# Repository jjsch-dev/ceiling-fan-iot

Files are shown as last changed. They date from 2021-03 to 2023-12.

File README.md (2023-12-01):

# Ceiling Fan Control - (No Humming)

The purpose of this project was to develop a hum-free electronic ceiling fan device that can be controlled remotely (IOT) or locally with a rotary encoder.

The selected processor was the [ESP32-C3](https://www.espressif.com/sites/default/files/documentation/esp32-c3-mini-1_datasheet_en.pdf) in its mini development kit format.

## Explode view 

As the purpose was to replace an old controller in my house, to fit it into a 100mm wall box I had to build a PCB to reduce footprint and use a 3D printer for the front cover that would fit a standard frame for electricity.

As in linux there is no support for fusion 360 use onshape to model the [assembly](https://cad.onshape.com/documents/71acf9008c56a0b1a5695f37/w/967222a47d34025a139e3862/e/0c178ba322c00475acc6add3) and cads of the [front cover](https://cad.onshape.com/documents/136d4c7a6a8e92c2be45bf03/w/4c451ab5564fe96ef80b367c/e/ab9c2ed234f4e64b43c2f324) which only requires a browser, and the result is amazing. And to design and manufacture the [PCB](https://easyeda.com/juanschiavoni/ceiling-iot-esp32-c3) use easyeda, the manufacturing service is good, but I could not export the pcba in step format, I had to use kicad.



## Electronic for No Humming

To prevent humming, capacitive reactances are used to limit the current in the motor stator, and since the friction (blades etc) is moderately high, the rotation speed decreases. This version has four speeds to keep the form factor as small as possible, (capacitors and relays are large).

## IOT Control

To control the device from a cell phone, [Espressif Rainmaker](https://rainmaker.espressif.com/docs/get-started.html) is used, which has an application for android and iphone, which allows you to configure the Wi-Fi network (provisioning), and control the device through the AWS IOT.

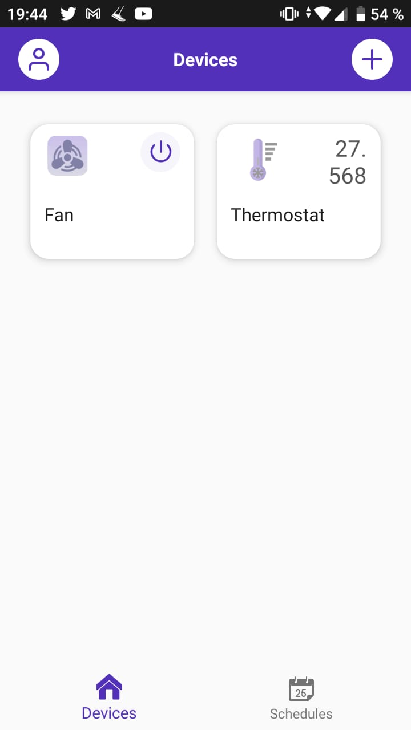
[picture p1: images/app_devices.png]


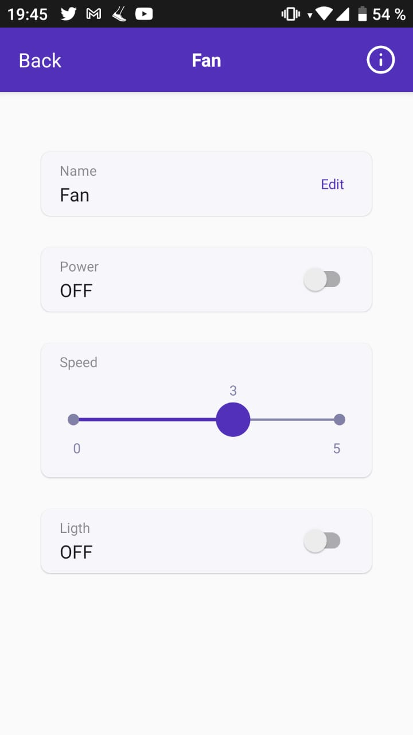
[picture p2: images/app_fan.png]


### Manual Control

For local control, a pushbutton rotary encoder is used to set the speed and turn the fan light on/off. To improve the speed resolution, the user has to rotate the shaft three or more steps to increase/decrease.

### Visual indication

Taking advantage of the fact that the ESP32-C3 mini board has a neopixel, the combinations of functions are indicated with colors and brightness levels. For example, when the light is off, the fan speed is indicated with 4 levels of brightness in red, but when it is on in green, and when the fan is off and the light on it turns blue to the maximum, and in idle the the led is white.

### Thermostat Device

Controls the (ON / OFF) of the fan with temperature. As a sensor it uses a thermistor of 100K at 25 degrees Celsius with a beta of 4250 from Murata model NXRT15WF104FA1B040. The firmware uses the simplified [Steinhart equation](https://en.wikipedia.org/wiki/Steinhart%E2%80%93Hart_equation) to linearize the response. The control implements a 2 degree hysterisis to improve system stability.

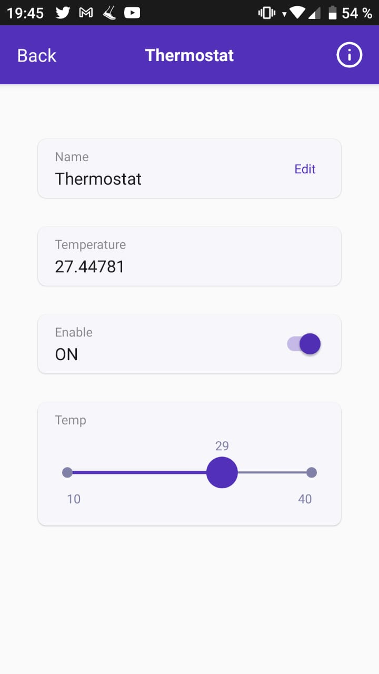
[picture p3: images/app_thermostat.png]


The [MF52A104F3950](https://datasheet.lcsc.com/lcsc/1810171512_Nanjing-Shiheng-Elec-MF52A104F3950-A1_C13424.pdf) thermistor that I end up using in the final product is different than the one I used in the prototype, but the results are similar to what I got with the Murata, below is a video with the measurements. Click to play in Youtube

(https://www.youtube.com/watch?v=cc-UPIDVQn8 "Click to play in Youtube")

### Power Supply

To power the electronic equipment, approximately 350 mA at 3.3V is required for the CPU when Wi-Fi is in active mode, and 90 mA at 5V for each relay. (350mA * 3.3V) = 1,155 W + (90 mA * 5 * 3 relays) = 1,350 W, total = 2,505 W. To increase the safety factor for the proof of concept select the Hi-Link source [HLK-5M05](https://datasheet.lcsc.com/szlcsc/1912111437_HI-LINK-HLK-5M05_C209907.pdf) that delivers 5V at 1A which is twice the estimated power.

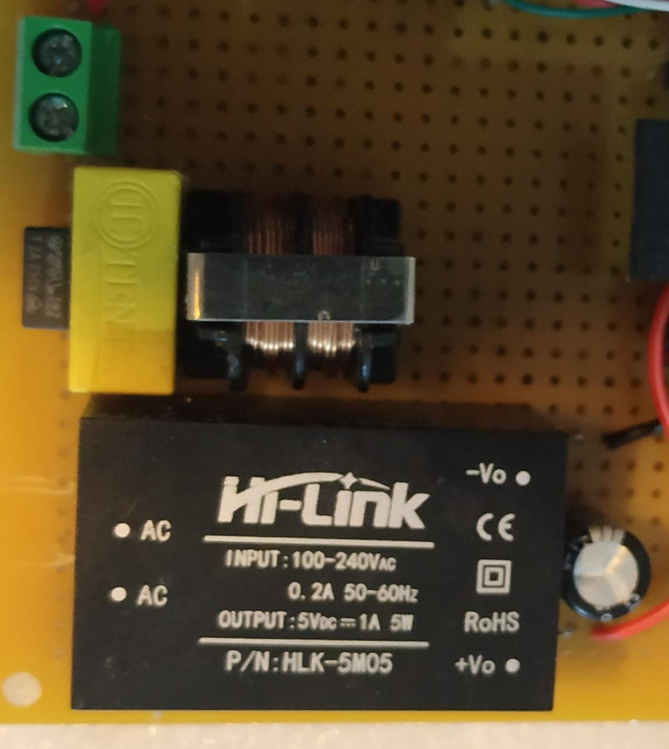
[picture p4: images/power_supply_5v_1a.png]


On page 7 of the datasheet, there is a table of suggestions for additional components such as a fuse to protect the circuit from damage when the module malfunctions, a capacitor for filtering and safety protection (EMC certified), and a filter / inductor in common. mode, for EMI filtering. And the last thing was adding a filter capacitor that can reduce the output ripple from the original 50mV to 30mV.

The next two images show the DC output and ripple output of the power supply without load.

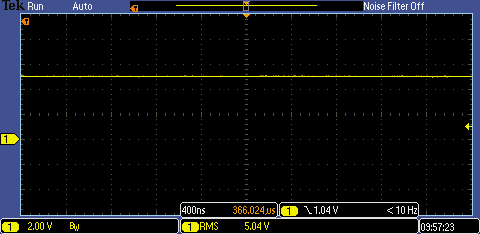
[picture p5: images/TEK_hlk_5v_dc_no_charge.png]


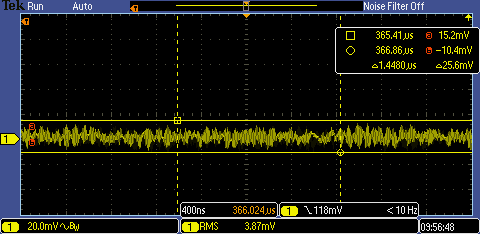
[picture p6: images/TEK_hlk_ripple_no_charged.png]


The next two pictures show the DC output and ripple output of the power supply with the CPU running.

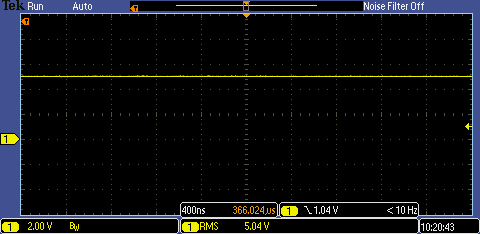
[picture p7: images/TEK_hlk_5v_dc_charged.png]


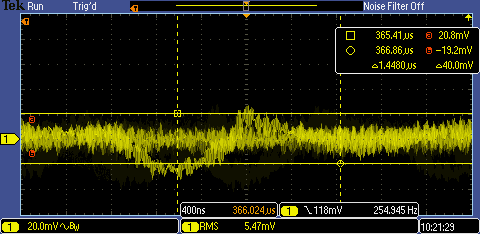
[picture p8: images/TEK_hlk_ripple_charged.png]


### Reset to Factory

Press and hold the encoder button for more than 3 seconds to reset the board to factory defaults. You will have to provision the board again to use it.

### Schematic

The schematic of the ESP32-C3 version is simple, it consists of an output stage made up of 4 relays, an encoder for manual control, and a thermistor to control the thermostat. As a power supply it uses a 5V 600 mA HLK.

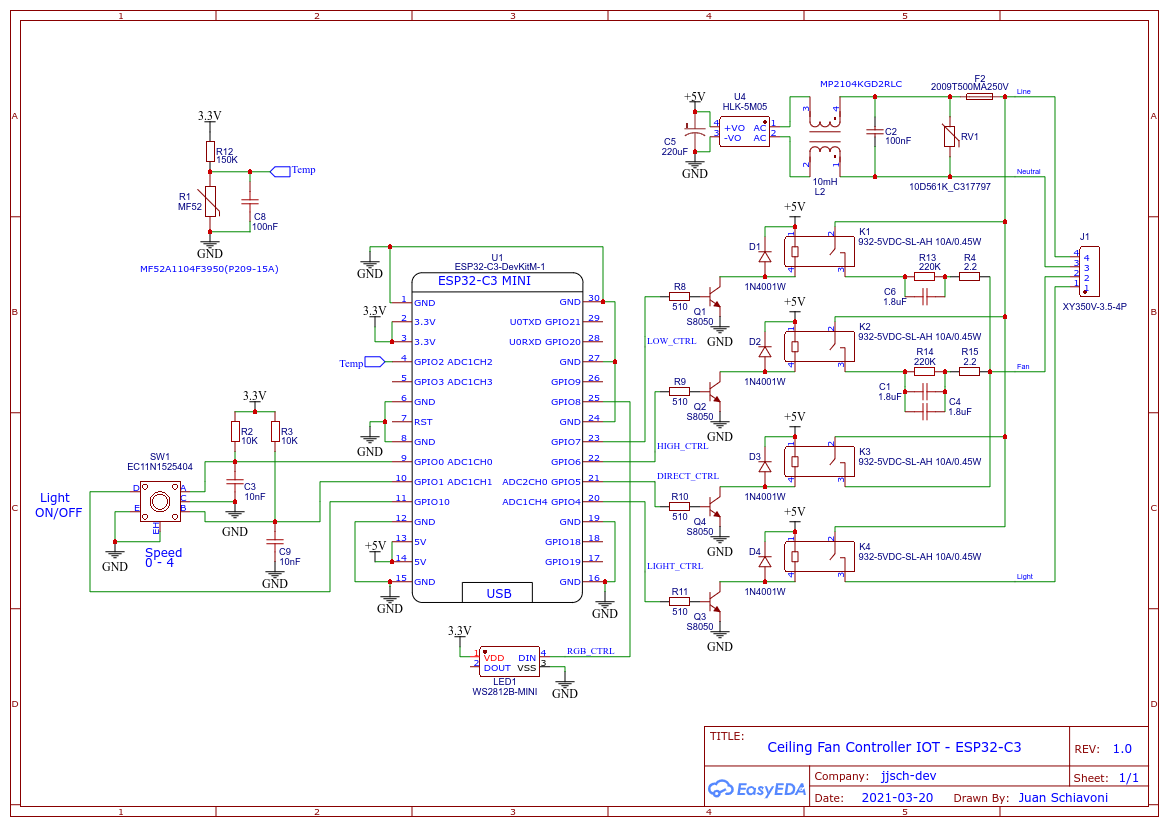
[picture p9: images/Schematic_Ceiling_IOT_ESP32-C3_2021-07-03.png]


### Prototype Board

The first version of the prototype is a mix of Arduino boards with conventional electronics. The next version will add a power supply to test the concept on a fan.

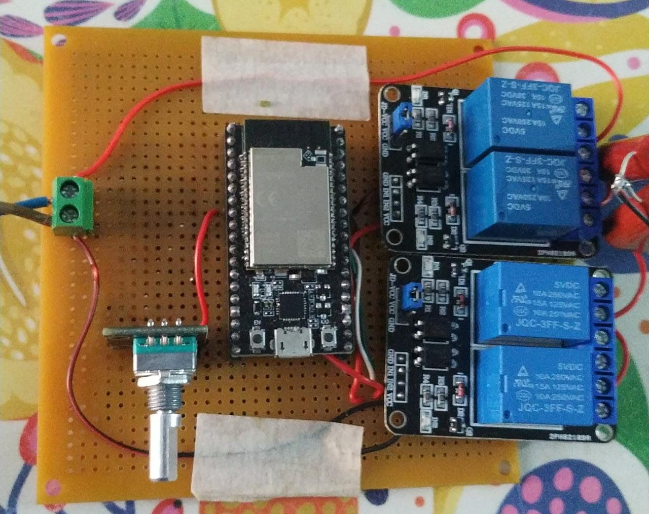
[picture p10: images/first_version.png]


The second version has the thermistor to control the fan thermostat.

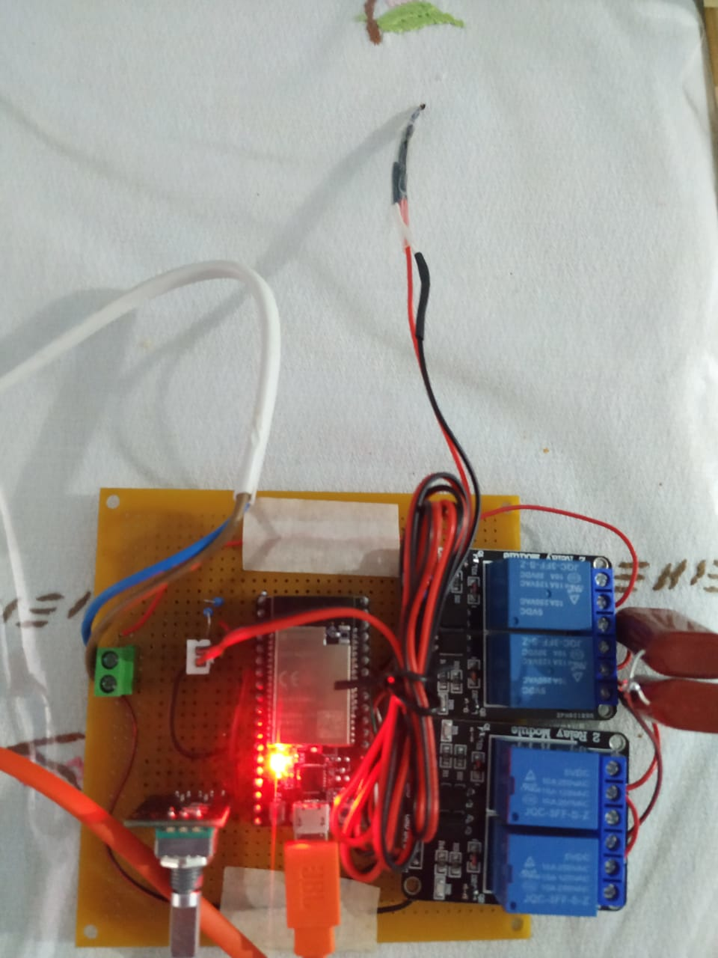
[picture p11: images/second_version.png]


The third prototype is already functional and, although the form factor is not suitable for a wall mount, it allows to control the fan with all the specified functionalities. As you can see, it uses the ESP32-C3 version of the CPU.

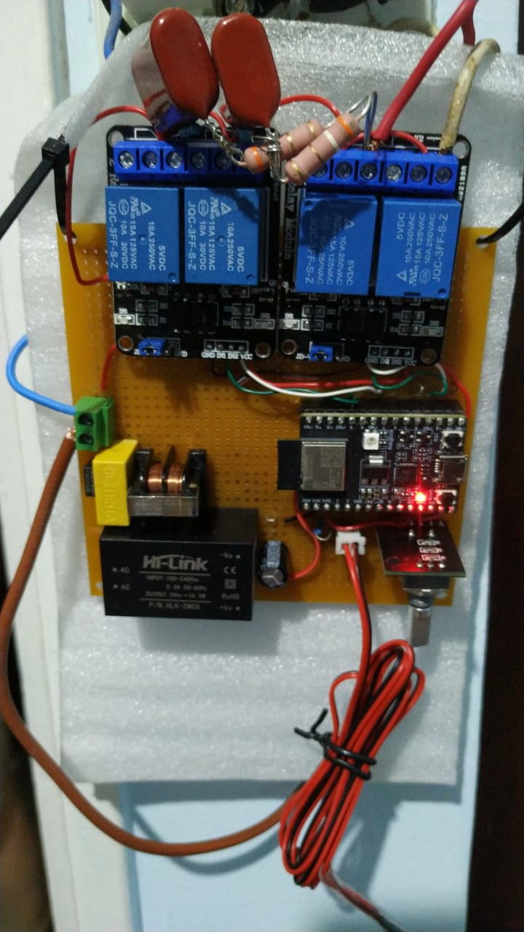
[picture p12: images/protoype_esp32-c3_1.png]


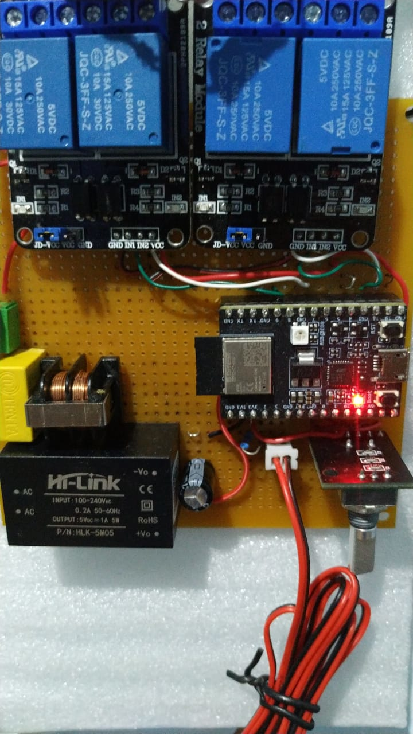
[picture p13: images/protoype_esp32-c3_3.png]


The fourth prototype was to test a smaller relay that is essential for the equipment to fit in a 100mm box. Therefore, a test had to be performed with the new [932-5VDC-SL-AH 10A/0.45W](https://datasheet.lcsc.com/lcsc/1912112237_NHLC-932-5VDC-SL-AH-10A-0-45W_C396979.pdf) relays to verify that they withstand current pulses when fan speeds change. NOTE: Sorry, but since the photo was taken after the final PCBA was assembled, it doesn't have the ESP32-C3 processor.

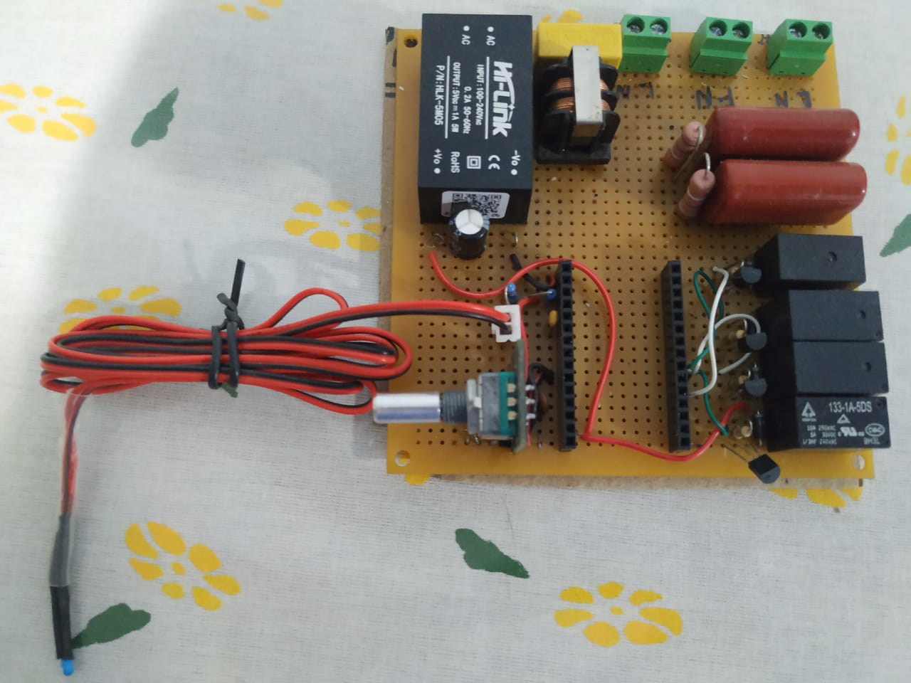
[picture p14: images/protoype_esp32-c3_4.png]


Below is a video of the test performed to evaluate the new relays. Click to play in Youtube.

(https://www.youtube.com/watch?v=B1B9G1hrwu8 "Click to play in Youtube")

### Final PCBA

To design and manufacture the PCB I used the easyeda online service, which allows you to buy at least 5 units, in my case it works because I plan to replace 4 old fan controllers and I also wanted to experience what the import process is like in my country.

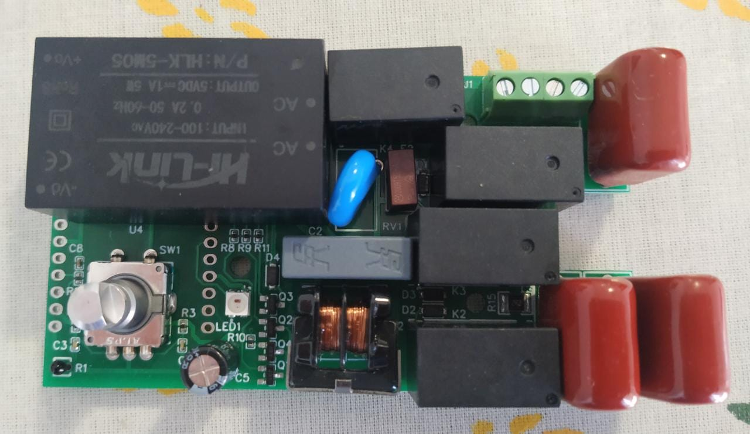
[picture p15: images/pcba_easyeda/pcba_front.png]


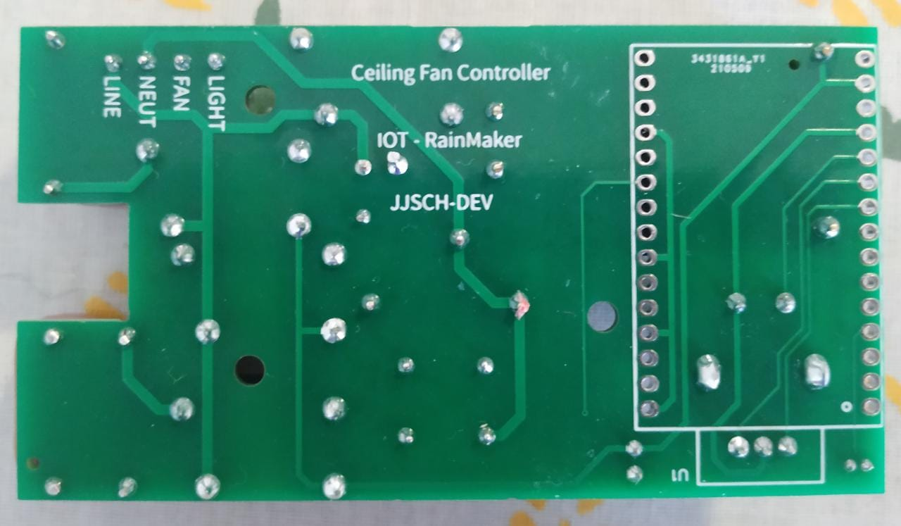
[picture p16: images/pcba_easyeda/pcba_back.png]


In this [link](https://easyeda.com/juanschiavoni/ceiling-iot-esp32-c3) you can access the project that is free under the MIT license, to reform it to your space needs, or if it works for you, you can order it directly from easyeda.

Images of the PCB mounted on the frame for the 100 mm deep-drawn box, typical of Argentina.

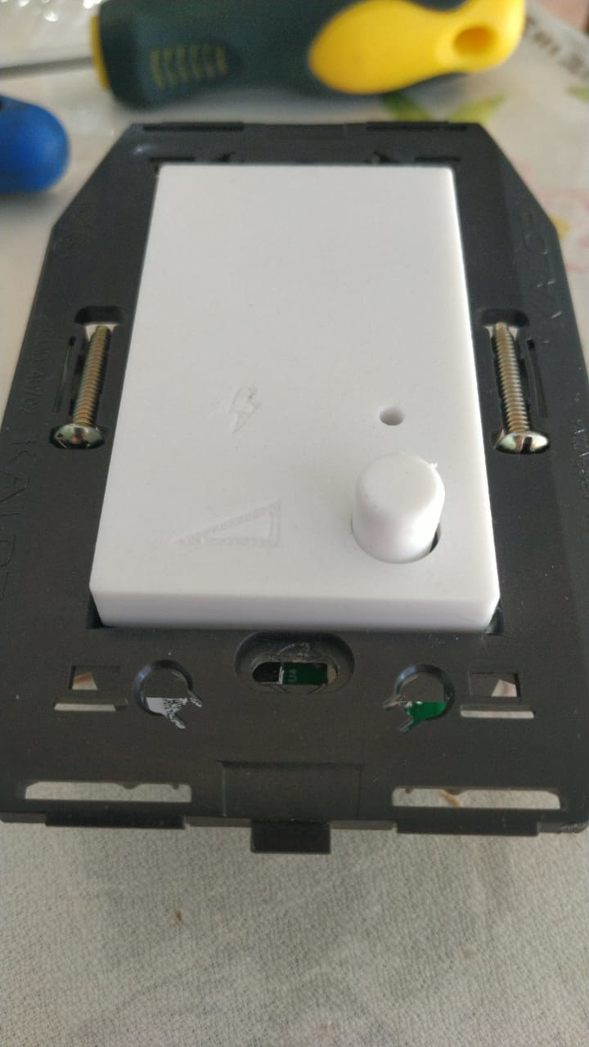
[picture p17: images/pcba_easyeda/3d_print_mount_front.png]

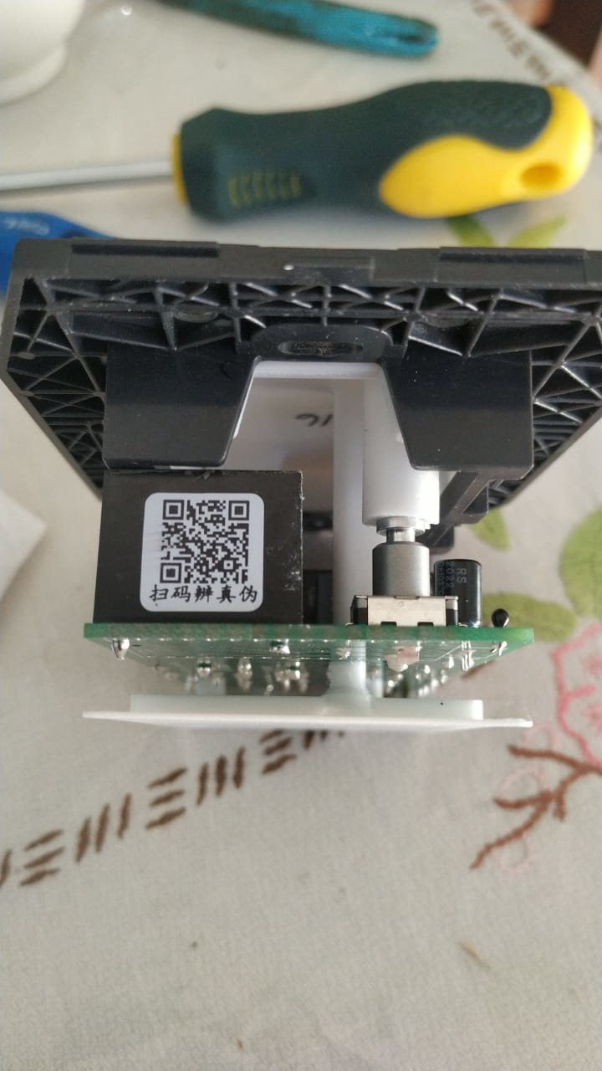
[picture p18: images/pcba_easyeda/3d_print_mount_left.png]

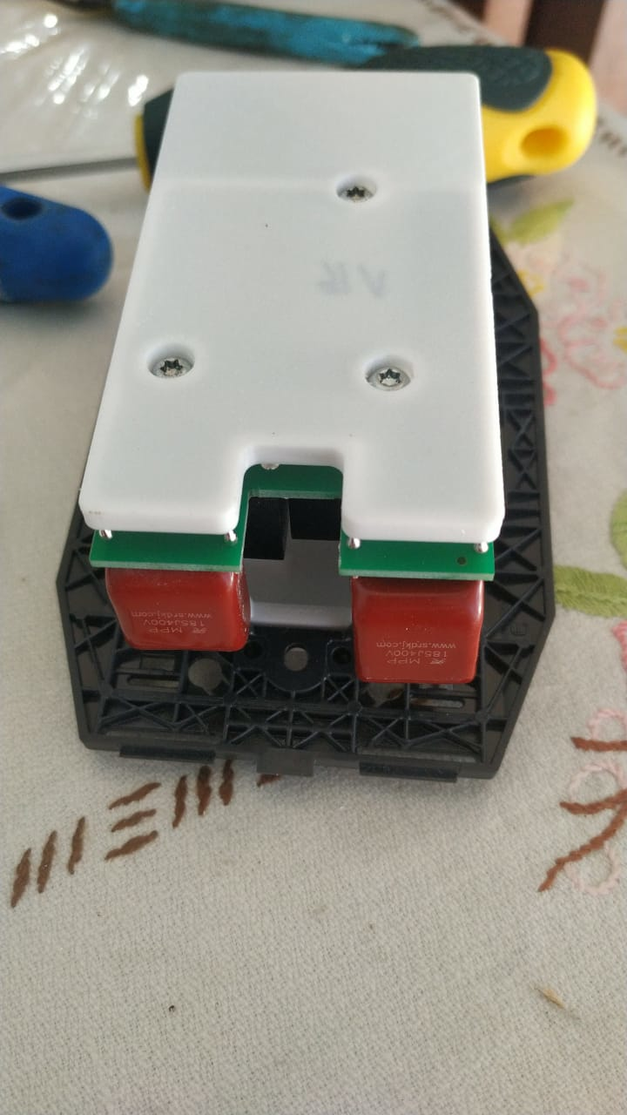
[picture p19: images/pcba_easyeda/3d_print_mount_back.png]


### PCBA order proccess

The following video shows the steps to be taken to order the boards with the assembled components except for the esp32-c3 processor, because for now they only mount one side of the PCB. Click to play in Youtube.

(https://www.youtube.com/watch?v=jPR6EYx1I08 "Click to play in Youtube")

### 3D print parts

To mount the pcba in the commercial rack, design with onshape a [cabinet front](https://cad.onshape.com/documents/136d4c7a6a8e92c2be45bf03/w/4c451ab5564fe96ef80b367c/e/ab9c2ed234f4e64b43c2f324) that with three screws allows mounting the board with a protector to avoid short circuits in metal boxes.
In total, 3 pieces are required to be printed in petg: the front, the knob and the protector.

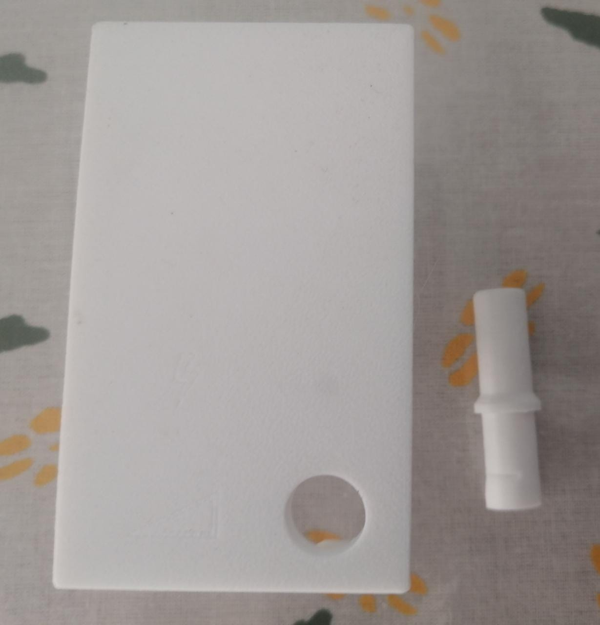
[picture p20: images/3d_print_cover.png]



### Development environment

The application is written in C, based on Espressif IDF and as a development tool the [Visual Code](https://docs.espressif.com/projects/esp-idf/en/latest/esp32/get-started/vscode-setup.html) of MS was used with the Espressif plugin.

* 1 Download the [IDF](https://docs.espressif.com/projects/esp-idf/en/latest/esp32/get-started/).

* 2 Download the [Rainmaker](https://github.com/espressif/esp-rainmaker).

* 3 Download the [celing-fan-iot](https://github.com/jjsch-dev/ceiling-fan-iot) application code.

* 4 Select the device target CPU for ESP32-C3.
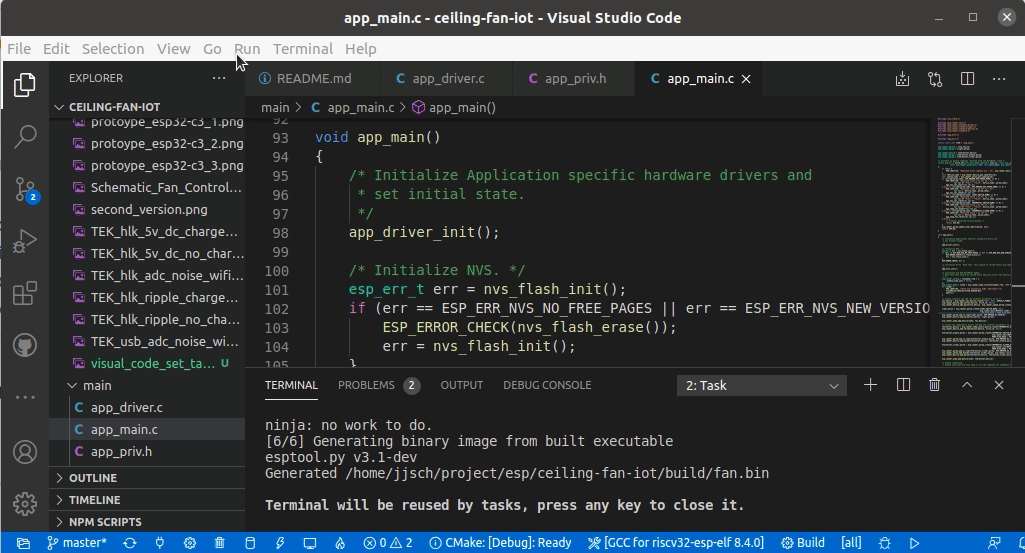
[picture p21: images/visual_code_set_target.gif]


* 5 Build (compile and link).
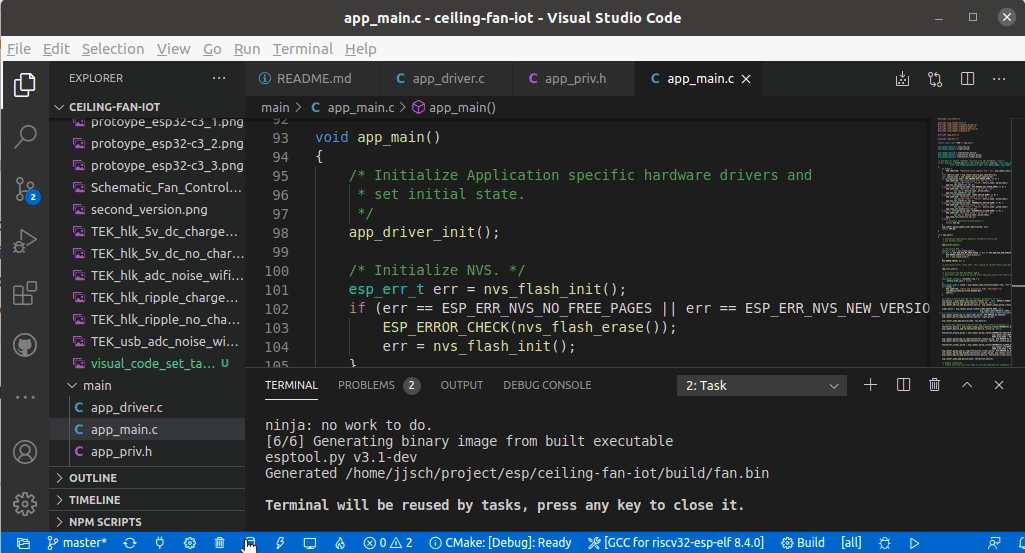
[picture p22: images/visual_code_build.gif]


* 6 Flash the code with visual code.
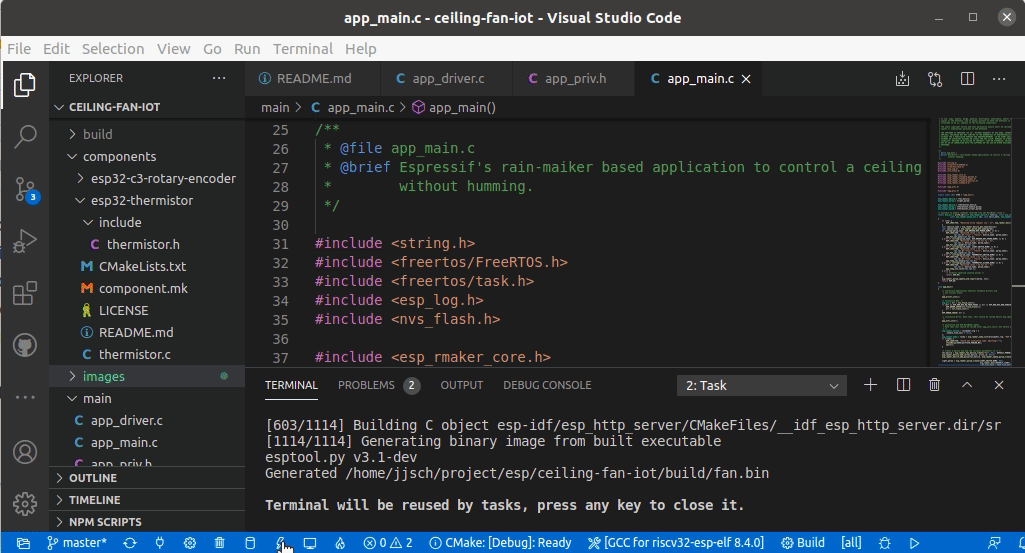
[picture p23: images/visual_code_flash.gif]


* 6.1 Flash the code with esptool
* 6.1.1 Download the bin files from [bin](https://github.com/jjsch-dev/ceiling-fan-iot/tree/master/bin) folder.
    
* 6.1.2 Use esptool to update the CPU with the following command line.
> python -m esptool --chip esp32c3 -b 460800 --before default_reset --after hard_reset write_flash --flash_mode dio --flash_size 4MB --flash_freq 80m 0x0 bin/bootloader.bin 0x8000 bin/partition-table.bin 0x16000 bin/ota_data_initial.bin 0x20000 bin/fan.bin

* 7 Run the serial monitor.
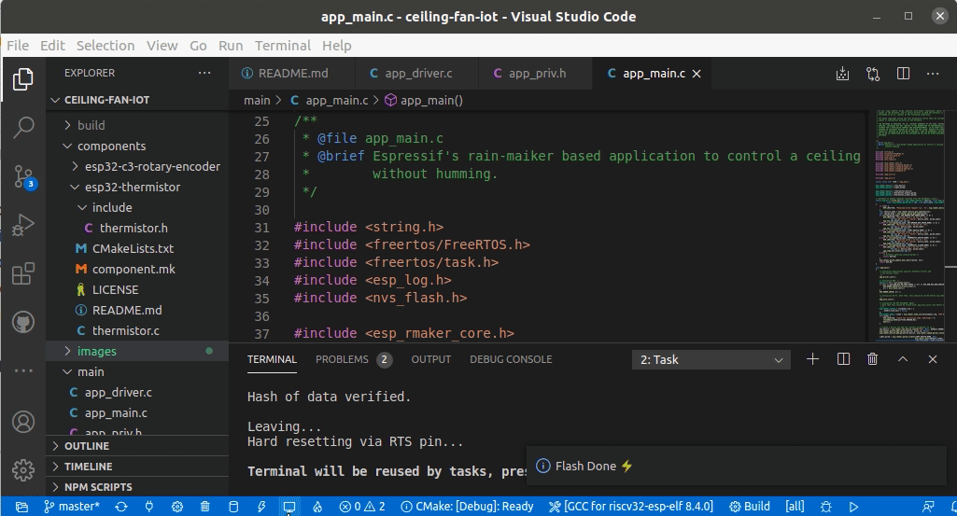
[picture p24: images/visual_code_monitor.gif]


* 8 Download the Rain-Maker application for Android or iPhone.

* 9 Provisioning (Configure and connect to the Wi-Fi network) Click to play in Youtube.

(https://youtu.be/cgpIMO7QH-g "Click to play in Youtube")

(https://youtu.be/ymNhdFpC66I "Click to play in Youtube")

* 10 Enjoy. Click to play in Youtube

(https://www.youtube.com/watch?v=VVv3FSHKODo "Click to play in Youtube")

### Testing the final controller

It shows how the ceiling fan can be controlled from the rainmaker cell phone APP that is connected to the AWS network. Click to play in Youtube.

(https://www.youtube.com/watch?v=gEUzPvxm420 "Click to play in Youtube")

It shows how the ceiling fan can be controlled manually. Click to play in Youtube.

(https://www.youtube.com/watch?v=aZ0LPAEYysA "Click to play in Youtube")

### Old ceiling controller

For reference, this was the bulky externally mounted ceiling fan light speed controller.

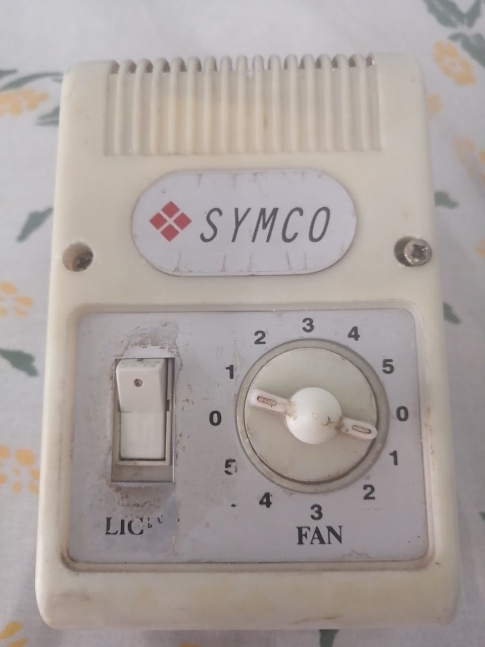
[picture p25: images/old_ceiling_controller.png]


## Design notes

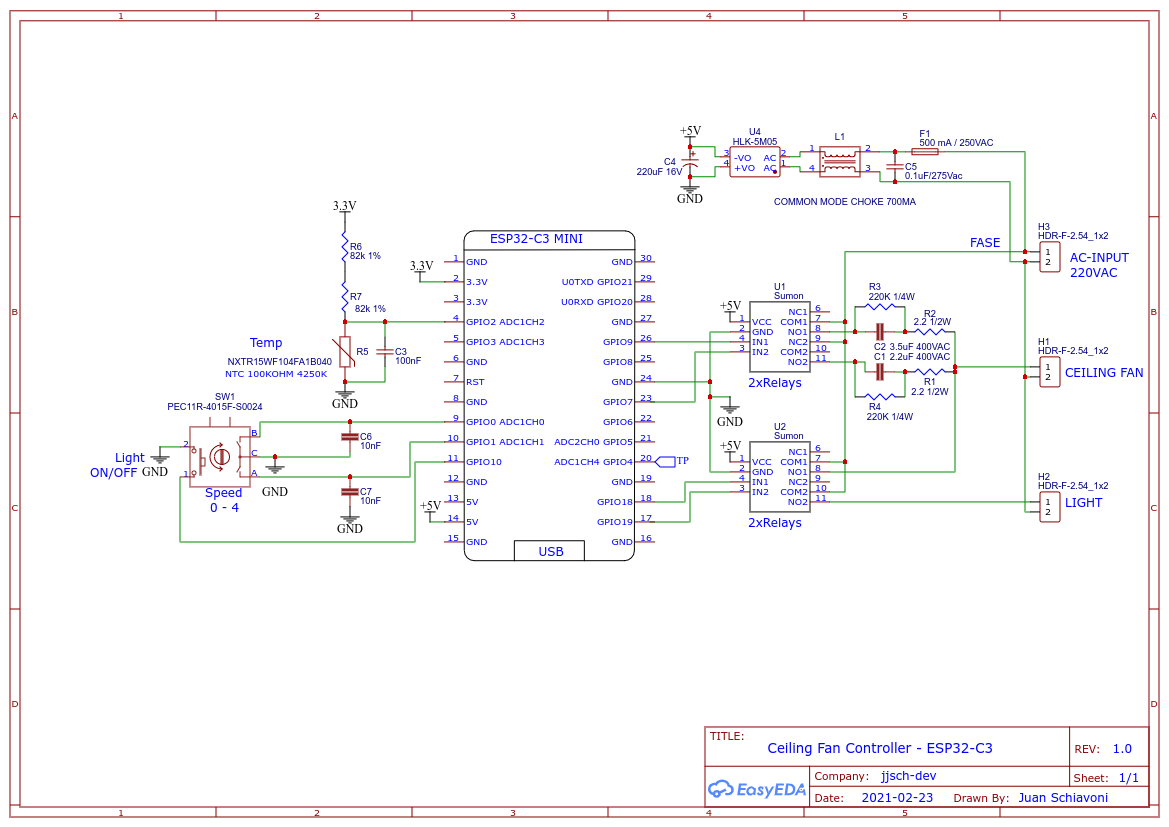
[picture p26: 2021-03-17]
images/Schematic_Fan_Controller_ESP32-C3.png

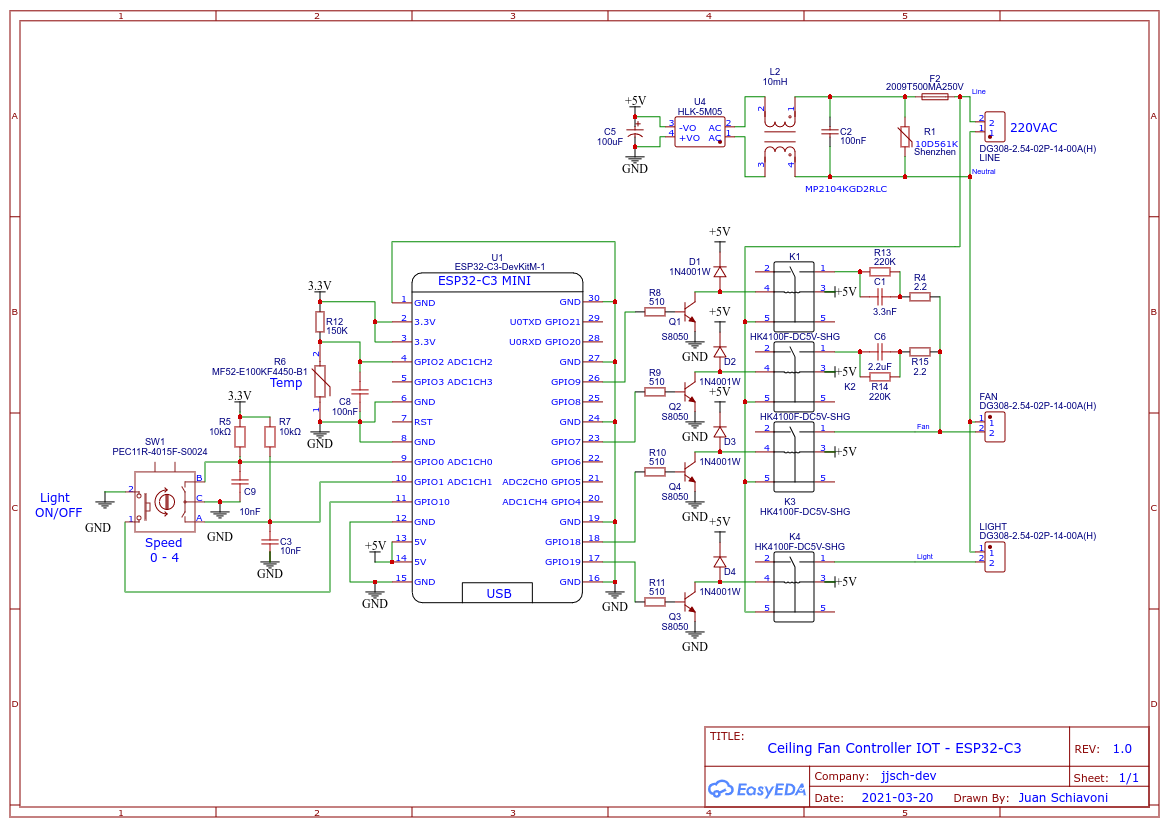
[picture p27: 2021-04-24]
images/Schematic_Ceiling_IOT_ESP32-C3_2021-03-24.png

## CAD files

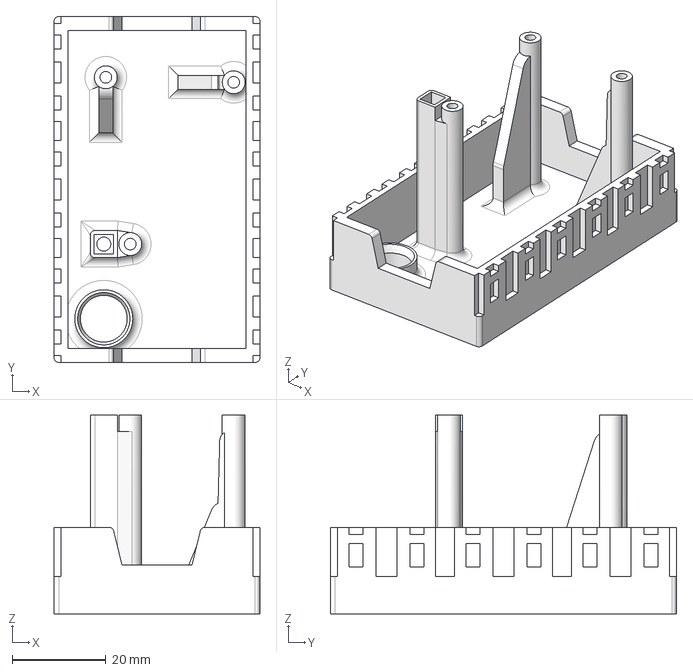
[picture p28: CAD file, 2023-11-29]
celing_fan_3d_parts/tapa_kalop_v4.step
44.0 x 74.0 x 42.5 mm

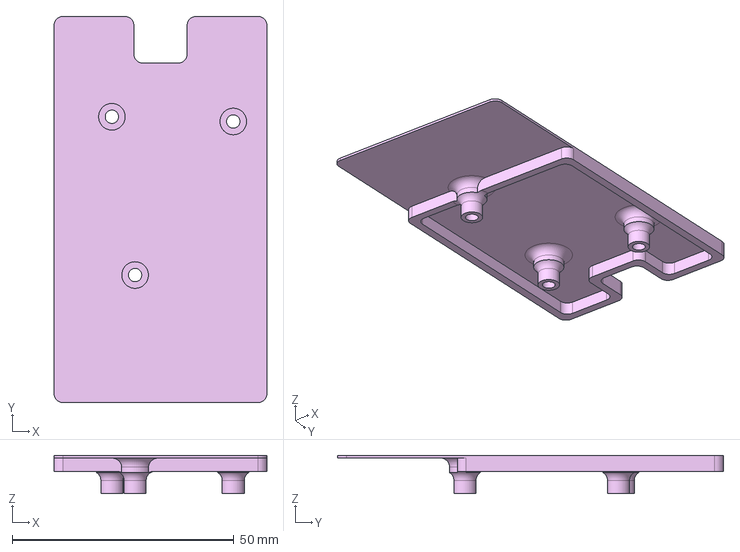
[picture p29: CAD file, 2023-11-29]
celing_fan_3d_parts/protector_pcb_v3.step
48.0 x 87.0 x 8.60 mm

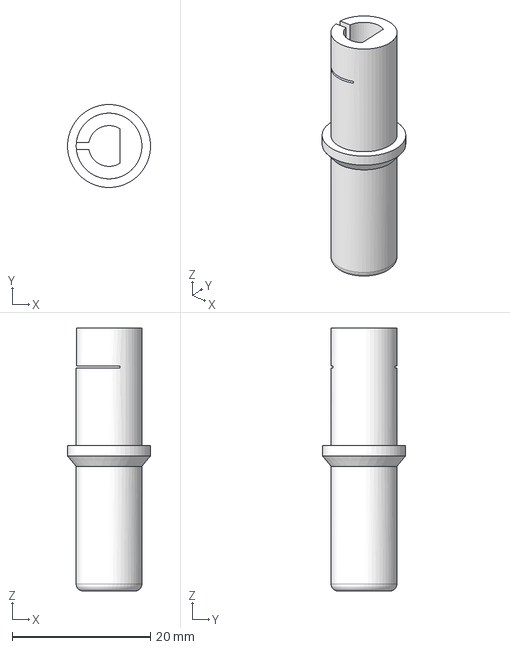
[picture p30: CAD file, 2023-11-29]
celing_fan_3d_parts/perilla_speed_alps.step
12.0 x 12.0 x 38.0 mm

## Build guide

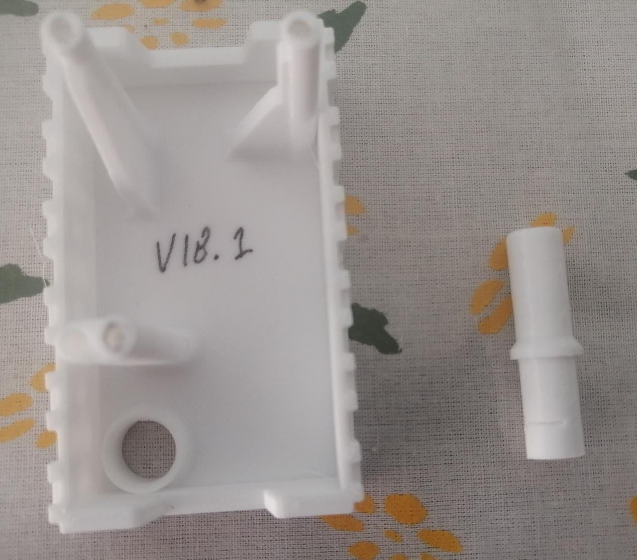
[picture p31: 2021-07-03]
images/3d_print_cover_perilla.png

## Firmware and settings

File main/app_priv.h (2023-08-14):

/*
 * MIT License
 * 
 * Copyright (c) 2021 Juan Schiavoni
 * 
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
 * THE SOFTWARE IS PROVIDED "AS IS", WITHOUT WARRANTY OF ANY KIND, EXPRESS OR
 * IMPLIED, INCLUDING BUT NOT LIMITED TO THE WARRANTIES OF MERCHANTABILITY,
 * FITNESS FOR A PARTICULAR PURPOSE AND NONINFRINGEMENT. IN NO EVENT SHALL THE
 * AUTHORS OR COPYRIGHT HOLDERS BE LIABLE FOR ANY CLAIM, DAMAGES OR OTHER
 * LIABILITY, WHETHER IN AN ACTION OF CONTRACT, TORT OR OTHERWISE, ARISING FROM,
 * OUT OF OR IN CONNECTION WITH THE SOFTWARE OR THE USE OR OTHER DEALINGS IN THE
 * SOFTWARE.
 */
#pragma once
#include <stdint.h>
#include <stdbool.h>

#define DEFAULT_POWER                       false
#define DEFAULT_SPEED                       3
#define DEFAULT_LIGHT                       false
#define DEFAULT_TEMPERATURE                 25.0
#define DEFAULT_THERMOSTAT_TEMPERATURE      30
#define DEFAULT_THERMOSTAT_ENABLE           false
#define TEMPERATURE_REPORTING_PERIOD        60 /* Seconds */
#define MAX_CELING_SPEED                    5

#define LIGHT_SWITCH_NAME                   "Ligth"
#define THERMOSTAT_DEVICE_NAME              "Thermostat"
#define THERMOSTAT_SWITCH_NAME              "Enable"
#define THERMOSTAT_SLIDER_NAME              "Temp"

extern esp_rmaker_device_t *fan_device;
extern esp_rmaker_param_t *light_param;

extern esp_rmaker_device_t *thermostat_device;
extern esp_rmaker_param_t *thermostat_enable_param;
extern esp_rmaker_param_t *thermostat_slider_param;

/**
 * @brief Initializes the encoder, the thermistor, the relays and the led.
 * @param void.
 */
void app_driver_init(void);

/**
 * @brief Turn the ceiling fan on and off.
 * @param power True = ON.
 *  
 * @return ESP_OK if successful
 */
esp_err_t app_fan_set_power(bool power);


/**
 * @brief TControl the fan speed.
 * @param Ceiling speed. 0 = turn off, 4 = max.
 *  
 * @return ESP_OK if successful
 */
esp_err_t app_fan_set_speed(uint8_t speed);

/**
 * @brief Turn the fan light on and off.
 * @param state True = ON
 *  
 * @return ESP_OK if successful
 */
esp_err_t app_fan_set_ligth(bool state);

/**
 * @brief Get the current temperature..
 * @param void
 *  
 * @return Celsius degrees.
 */
float app_get_current_temperature(void);

/**
 * @brief Enable temperature fan control.
 * @param enable True = Enabled
 */
void app_temp_set_enable(bool enable);

/**
 * @brief Set the thermostat temperature.
 * @param level = 20 to 50 Celsius degree.
 */
void app_temp_set_level(int level);

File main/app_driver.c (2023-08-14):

/*
 * MIT License
 * 
 * Copyright (c) 2021 Juan Schiavoni
 * 
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
 * THE SOFTWARE IS PROVIDED "AS IS", WITHOUT WARRANTY OF ANY KIND, EXPRESS OR
 * IMPLIED, INCLUDING BUT NOT LIMITED TO THE WARRANTIES OF MERCHANTABILITY,
 * FITNESS FOR A PARTICULAR PURPOSE AND NONINFRINGEMENT. IN NO EVENT SHALL THE
 * AUTHORS OR COPYRIGHT HOLDERS BE LIABLE FOR ANY CLAIM, DAMAGES OR OTHER
 * LIABILITY, WHETHER IN AN ACTION OF CONTRACT, TORT OR OTHERWISE, ARISING FROM,
 * OUT OF OR IN CONNECTION WITH THE SOFTWARE OR THE USE OR OTHER DEALINGS IN THE
 * SOFTWARE.
 */

/**
 * @file app_driver.c
 * @brief Based on the Espressif example, it implements the low-level drivers 
 *        that control the fan (relays / thermistor, led).
 */

#include <sdkconfig.h>

#include <iot_button.h>
#include <esp_rmaker_core.h>
#include <esp_rmaker_standard_types.h> 
#include <esp_rmaker_standard_params.h> 

#include <app_reset.h>
#include "app_priv.h"

#include "rotary_encoder.h"
#include "thermistor.h"
#include "math.h"

#include "esp_log.h"
static const char* TAG = "app_drv";

#ifdef CONFIG_IDF_TARGET_ESP32C3
    #include <ws2812_led.h>
#endif

/* This is the button that is used for toggling the power */
#define BUTTON_GPIO          CONFIG_ROT_ENC_BUTTON_GPIO
#define BUTTON_ACTIVE_LEVEL  0

#define WIFI_RESET_BUTTON_TIMEOUT       30
#define FACTORY_RESET_BUTTON_TIMEOUT    60

static uint8_t g_speed = DEFAULT_SPEED;
static bool g_power = DEFAULT_POWER;
static bool g_light = DEFAULT_LIGHT;
static float g_temperature = 0;
static bool g_temp_enable = DEFAULT_THERMOSTAT_ENABLE;
static int g_temp_level = DEFAULT_THERMOSTAT_TEMPERATURE;

// Create rotary encoder instance, and timer
static esp_timer_handle_t temperature_timer;
static rotenc_handle_t h_encoder = { 0 };

static thermistor_handle_t th;
static int32_t last_encoder_position = 0; 

// Converts the choice of menuconfig into the enums of the ADC channels.
#if CONFIG_ADC_CHANNEL_1
	#define THERMISTOR_ADC_CHANNEL ADC_CHANNEL_1
#elif CONFIG_ADC_CHANNEL_2
	#define THERMISTOR_ADC_CHANNEL ADC_CHANNEL_2
#elif CONFIG_ADC_CHANNEL_3
	#define THERMISTOR_ADC_CHANNEL ADC_CHANNEL_3
#elif CONFIG_ADC_CHANNEL_4
	#define THERMISTOR_ADC_CHANNEL ADC_CHANNEL_4
#elif CONFIG_ADC_CHANNEL_5
	#define THERMISTOR_ADC_CHANNEL ADC_CHANNEL_5
#elif CONFIG_ADC_CHANNEL_6
	#define THERMISTOR_ADC_CHANNEL ADC_CHANNEL_6
#elif CONFIG_ADC_CHANNEL_7
	#define THERMISTOR_ADC_CHANNEL ADC_CHANNEL_7
#elif CONFIG_ADC_CHANNEL_8
	#define THERMISTOR_ADC_CHANNEL ADC_CHANNEL_8
#elif CONFIG_ADC_CHANNEL_9
	#define THERMISTOR_ADC_CHANNEL ADC_CHANNEL_9
#else
    #error "Configure the ADC channel where the thermistor is connected"
#endif

/**
 * @brief Activates the corresponding relay and applies the configured logic.
 */
static void relay_on(gpio_num_t gpio_num)
{
bool level = true;  

#if CONFIG_ACTIVATE_RELAY_LOW
    level = false;
#endif
   
   gpio_set_level(gpio_num, level);
}

/**
 * @brief Turn off the corresponding relay and apply the configured logic.
 */
static void relay_off(gpio_num_t gpio_num)
{
bool level = false;  

#if CONFIG_ACTIVATE_RELAY_LOW
    level = true;
#endif
   
   gpio_set_level(gpio_num, level);
}

static void set_idle_color(void)
{
    ws2812_led_set_rgb((0xCC/3), (0xCC/3), (0x99/3)); 
}

/**
 * @brief Initialize the LED driver, with the ESP32-C3-Devkitm a neopixel 
 *        is used.
 */
static esp_err_t init_led(void)
{
esp_err_t err = ESP_OK;

#ifdef CONFIG_IDF_TARGET_ESP32C3
    err = ws2812_led_init();
    if (err == ESP_OK) {
        set_idle_color();
    }
    ESP_LOGI(TAG, "ws2812_led_init -1: %d", err);
#endif
    return err;
}

/**
 * @brief Re-maps a number from one range to another. That is, a value of fromLow 
 *        would get mapped to toLow, a value of fromHigh to toHigh, values in-between 
 *        to values in-between, etc.
 *        NOTE: this function was inspired by Arduino: 
 *        https://www.arduino.cc/reference/en/language/functions/math/map/
 * 
 * @param x The number to map.
 * @param in_min The lower bound of the value’s current range.
 * @param in_max The upper bound of the value’s current range.
 * @param out_min The lower bound of the value’s target range.
 * @param out_max The upper bound of the value’s target range
 * @return The mapped value.
.*/
static uint32_t num_map(uint32_t x, 
                        uint32_t in_min, uint32_t in_max, 
                        uint32_t out_min, uint32_t out_max) 
{
    return (x - in_min) * (out_max - out_min) / (in_max - in_min) + out_min;
}

/**
 * @brief Use a neopixel to indicate controller status by modifying RGB colors 
 *        and level.
 * @param speed  Ceiling speed (0 to 5).
 * @param light  Light on or off.
 */
static void show_status(uint8_t speed, bool light)
{
#ifdef CONFIG_IDF_TARGET_ESP32C3
    uint32_t level = num_map(speed, 0, MAX_CELING_SPEED, 0, 100);
    // If the fan and the light are activated, it indicates the speed level in 
    // green, and when the light is off in red; If the fan is off and the light 
    // is on, the blue led turns on 100%.
    if ((speed > 0) && (g_power)) {
        if (light) { 
            ws2812_led_set_rgb(0, level, 0);
        } else {
            ws2812_led_set_rgb(level, 0, 0);  
        }
    } else if (light) {
        ws2812_led_set_rgb(0, 0, 100); 
    } else {
        set_idle_color();
    }
#endif
}

/**
 * @brief Control the relays to set the fan speed.
 * @param val Ceiling speed. 0 = turn off, 4 = max.
 */
static void set_speed(uint8_t val)
{
    // First turn off the relay.
    if (val == 0) {
        relay_off(CONFIG_RELAY_SPEED_CAP_LOW_GPIO);
        relay_off(CONFIG_RELAY_SPEED_CAP_HIGH_GPIO);
        relay_off(CONFIG_RELAY_SPEED_DIRECT_GPIO);
    } else if (val == 1) {
        relay_off(CONFIG_RELAY_SPEED_CAP_HIGH_GPIO);
        relay_off(CONFIG_RELAY_SPEED_DIRECT_GPIO);
        relay_on(CONFIG_RELAY_SPEED_CAP_LOW_GPIO);
    } else if (val == 2) {
        relay_off(CONFIG_RELAY_SPEED_CAP_LOW_GPIO);
        relay_off(CONFIG_RELAY_SPEED_DIRECT_GPIO);
        relay_on(CONFIG_RELAY_SPEED_CAP_HIGH_GPIO);
    } else if (val == 3) {
        relay_off(CONFIG_RELAY_SPEED_DIRECT_GPIO);
        relay_on(CONFIG_RELAY_SPEED_CAP_LOW_GPIO);
        relay_on(CONFIG_RELAY_SPEED_CAP_HIGH_GPIO);
    } else if ((val == 4) || (val == 5)) {
        relay_off(CONFIG_RELAY_SPEED_CAP_LOW_GPIO);
        relay_off(CONFIG_RELAY_SPEED_CAP_HIGH_GPIO);
        relay_on(CONFIG_RELAY_SPEED_DIRECT_GPIO);
    }

    show_status(val, g_light);
}
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

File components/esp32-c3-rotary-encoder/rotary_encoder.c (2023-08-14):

/*
 * MIT License
 * 
 * Copyright (c) 2021 Juan Schiavoni
 * 
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
 * THE SOFTWARE IS PROVIDED "AS IS", WITHOUT WARRANTY OF ANY KIND, EXPRESS OR
 * IMPLIED, INCLUDING BUT NOT LIMITED TO THE WARRANTIES OF MERCHANTABILITY,
 * FITNESS FOR A PARTICULAR PURPOSE AND NONINFRINGEMENT. IN NO EVENT SHALL THE
 * AUTHORS OR COPYRIGHT HOLDERS BE LIABLE FOR ANY CLAIM, DAMAGES OR OTHER
 * LIABILITY, WHETHER IN AN ACTION OF CONTRACT, TORT OR OTHERWISE, ARISING FROM,
 * OUT OF OR IN CONNECTION WITH THE SOFTWARE OR THE USE OR OTHER DEALINGS IN THE
 * SOFTWARE.
 */

/**
 * @file rotary_encoder.c
 * @brief Driver implementation Incremental Rotary Encoder component for ESP32-C3.
 */

#include "rotary_encoder.h"

#include "esp_log.h"

#define TAG "rotenc"

/**
 * @brief Toggle test pin to debug irqs events.
 * @param[in] void
 * @return void
 */
static void rotenc_toggle_test_pin(void)
{
#if CONFIG_TEST_PIN_ENABLE    
    gpio_set_level(CONFIG_ROT_ENC_TEST_PIN_GPIO, !gpio_get_level(CONFIG_ROT_ENC_TEST_PIN_GPIO));
#endif
}

/**
 * @brief Enable clock IRQ and disable data IRQ.
 * @param[in] arg Pointer to allocated rotary encoder instance.
 * @return void
 */
static void rotenc_enable_clk_irq(rotenc_handle_t * handle)
{
   gpio_intr_disable(handle->pin_dta);
   gpio_intr_enable(handle->pin_clk);
}

/**
 * @brief Disable clock IRQ and enable data IRQ.
 * @param[in] arg Pointer to allocated rotary encoder instance.
 * @return void
 */
static void rotenc_disable_clk_irq(rotenc_handle_t * handle)
{
    gpio_intr_disable(handle->pin_clk);
    gpio_intr_enable(handle->pin_dta);
}

/**
 * @brief When the anti-bounce timer expires, check that the sequence 
 *        (pin levels) is valid to update the rotary enconder status.
 * @param[in] arg Pointer to allocated rotary encoder instance.
 * @return void
 */
static void IRAM_ATTR rotenc_debounce_callback(void *arg)
{
    rotenc_handle_t * handle = (rotenc_handle_t*) arg;

    // Updates the rotation state, when the clock pin is low and 
    // the data pin level match the start state (when irq occurred).
    if (!gpio_get_level(handle->pin_clk) && 
       (handle->irq_data_level == gpio_get_level(handle->pin_dta))) {
        
        rotenc_toggle_test_pin();
        
        // Reverses rotation direction when flip is enabled.
        bool data_level = handle->irq_data_level ? true : false;
        if (data_level == !handle->flip_direction) {
            ++handle->state.position;
            handle->state.direction = ROTENC_CW;
        } else {
            --handle->state.position;
            handle->state.direction = ROTENC_CCW;
        }

        rotenc_event_t event = {
            .position = handle->state.position,
            .direction = handle->state.direction,
        };
        
        if (handle->q_event.queue) {
            xQueueOverwrite(handle->q_event.queue, &event);
        } else if (handle->event_callback) {
            handle->event_callback(event);
        }
    } else { 
        rotenc_enable_clk_irq(handle);
    }
}

/**
 * @brief Re-enable clock pin irq.
 * @param[in] args Pointer to allocated rotary encoder instance.
 * @return void
 */
static void IRAM_ATTR rotenc_isr_dta(void * args)
{
    rotenc_handle_t * handle = (rotenc_handle_t *)args;
    rotenc_enable_clk_irq(handle);
    esp_timer_stop(handle->debounce_timer);
    rotenc_toggle_test_pin();
}

/**
 * @brief It sets the anti-bounce timer each time it detects a falling edge.
 * @param[in] args Pointer to allocated rotary encoder instance.
 * @return void
 */
static void IRAM_ATTR rotenc_isr_clk(void * args)
{
    rotenc_handle_t * handle = (rotenc_handle_t *)args;
    rotenc_disable_clk_irq(handle);

    rotenc_toggle_test_pin();
  
    handle->irq_data_level = gpio_get_level(handle->pin_dta);

    esp_timer_stop(handle->debounce_timer);
    ESP_ERROR_CHECK(esp_timer_start_once(handle->debounce_timer, handle->debounce_us));       
}

/**
 * @brief When the anti-bounce timer expires, check if the button's callback function 
 * has already been invoked, and if the button is released to reactivate the irq.
 * @param[in] arg Pointer to allocated rotary encoder instance.
 * @return void
 */
static void IRAM_ATTR rotenc_button_timer_callback(void *arg)
{
    rotenc_handle_t * handle = (rotenc_handle_t*) arg;

    if( !handle->button.cb_invoked) {
        handle->button.cb_invoked = true;
        handle->button.callback(arg);
    } else if (gpio_get_level(handle->button.pin)) {
        gpio_set_intr_type(handle->button.pin, GPIO_INTR_NEGEDGE);
        return;
    }

    ESP_ERROR_CHECK(esp_timer_start_once(handle->button.timer, handle->button.debounce_us));
}

/**
 * @brief Set the anti-bounce timer to 10 uS and stop the IRQ. 
 *        NOTE: the button's callback function is invoked in the 
 *        timer to quickly release the IRQ.
 * @param[in] args Pointer to allocated rotary encoder instance.
 * @return void
 */
static void IRAM_ATTR rotenc_button_isr(void * args)
{
    rotenc_handle_t * handle = (rotenc_handle_t *)args;
    gpio_set_intr_type(handle->button.pin, GPIO_INTR_DISABLE);

    handle->button.cb_invoked = false;
    esp_timer_stop(handle->button.timer);
    ESP_ERROR_CHECK(esp_timer_start_once(handle->button.timer, 10)); 
}
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

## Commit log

2021-03-12 extend stack size for timer to 2560 - fix error.
2021-03-12 pin change for high speed cap, add LED indicator
2021-03-13 switch to ws2812_led_set_rgb to indicate speed
2021-03-14 show_status now shows push button
2021-03-14 synchronize states with the power variable.
2021-03-15 fix thermostat init values
    [app_driver.c, app_priv.h]
2021-03-17 Edit Readme for ESP32-C3
2021-03-17 fix c3 schematic
2021-03-17 fix schematic
2021-03-17 rename schematic
2021-03-17 add power supply
2021-03-17 fix power supply readme
2021-03-18 output capacitor for power supply
2021-03-18 add esp32-c3 to readme
2021-07-03 Readme - add assembly section
2021-07-03 add last schematic
2021-07-03 add last schematic image
2021-07-03 final rename schematic
2021-07-03 readme add final pcba
2021-07-03 readme - add 3d print section
2021-07-03 readme - fix links 3d print
2021-07-04 readme - thermistor measures
2021-07-04 readme - add pcba order steps.
2023-11-29 add kalop step model
    [perilla_speed_alps.step, protector_pcb_v3.step, tapa_kalop_v4.step]
